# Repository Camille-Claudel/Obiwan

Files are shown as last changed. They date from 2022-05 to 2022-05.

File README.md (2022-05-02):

# Introduction
Obiwan est un pointeur laser capable de s’orienter dans n’importe quelle direction.  

https://user-images.githubusercontent.com/80780126/166306557-4985dba1-e16e-4158-aaa8-b6b7efb4e9a4.mp4

## Contexte
Nous sommes le club d'informatique du lycée Camille Claudel avec environ 8 membres actifs. Étant un club très jeune et géré exclusivement par des élèves, nous sommes fiers de vous présenter ce projet, fait en quelques semaines avec un budget très réduit. Nous espérons que vous apprécierez lire cette présentation autant que nous avons apprécié réaliser ce projet !

## Objectifs
L’objectif principal est de pouvoir orienter le laser dans une direction arbitraire.  
Nous espérons ensuite pouvoir utiliser le dispositif pour dessiner un motif et le capturer à l’aide d’une photo à pose longue, à la manière du [light painting](https://fr.wikipedia.org/wiki/Light_painting).  
Enfin, si tous les objectifs précédents sont remplis, nous essayerons d’automatiser le contrôle du laser pour dessiner un motif à partir d’une image vectorielle.

# Principe de fonctionnement
Pour diriger le laser, nous utiliserons deux moteurs: l’un qui contrôle le mouvement gauche-droite, appelé azimut, et l’autre qui contrôle l'axe haut-bas, appelé altitude. Ce vocabulaire est emprunté au système de coordonnées céleste appelé “[système de coordonnées horizontales](https://fr.wikipedia.org/wiki/Syst%C3%A8me_de_coordonn%C3%A9es_horizontales)”, utilisé en astronomie:  
  
Pour photographier les motifs créés, nous utiliserons la technique du light painting. Elle consiste à prendre une photo avec un temps de pose (la durée pendant laquelle l’appareil photo capte de la lumière) relativement long, pour faire apparaître sur l’image la trajectoire du point lumineux.

# Problèmes rencontrés et solutions apportées

## Choix de fabrication/architecture
Le mouvement est contrôlé par des servomoteurs et une carte Arduino. Le moteur azimut entraîne une roue d’engrenage sur laquelle est positionné le moteur altitude. Le laser est scotché sur le moteur altitude. La structure est imprimée en 3D en PLA.  

  
Le moteur altitude est positionné au centre le son engrenage, ce qui fait que le laser a une excentricité par rapport à l’axe azimutal. La droite du rayon du laser n’est donc pas sécante avec l’axe de rotation azimutal.

## Excentricité
Cette excentricité conduit les dessins à être déformés. Pour y remédier, le programme prend en entrée les coordonnées du point visé, et calcule l’angle à donner aux moteurs pour le pointer malgré l’excentricité.  



## Précision
Au départ, nous dessinions sur un mur à environ 1.5m du laser. Le tracé manquait cependant de précision, car nos moteurs ont une précision de seulement environ 1 degré. Nous avons donc d’abord réduit la taille de l’engrenage de l’axe azimutal pour avoir une réduction 1:2, et ainsi avoir une précision de 0.5 degré. Cela a eu pour effet secondaire de rendre le dispositif plus compact.  

  
Cela n’a pas suffi à régler le problème, car la précision de l’axe altitude est restée la même, et même ces 0.5 degrés de précisions n’étaient pas suffisants. Nous avons alors réalisé que simplement rapprocher le dispositif de la surface de dessin augmentait grandement la précision, car les dessins faisaient alors plus de degrés de large.

## Rectilinéarité

Avec notre dispositif, nous pouvions pointer une position donnée, mais lors du déplacement d’une position à une autre le tracé n’était pas droit, car la vitesse des moteurs n’est pas constante. Pour tracer des segments, on pointe donc vers des positions intermédiaires.

En ajoutant plus de points intermédiaires, les traits sont plus rectilignes et plus uniformes.


# Résultat final


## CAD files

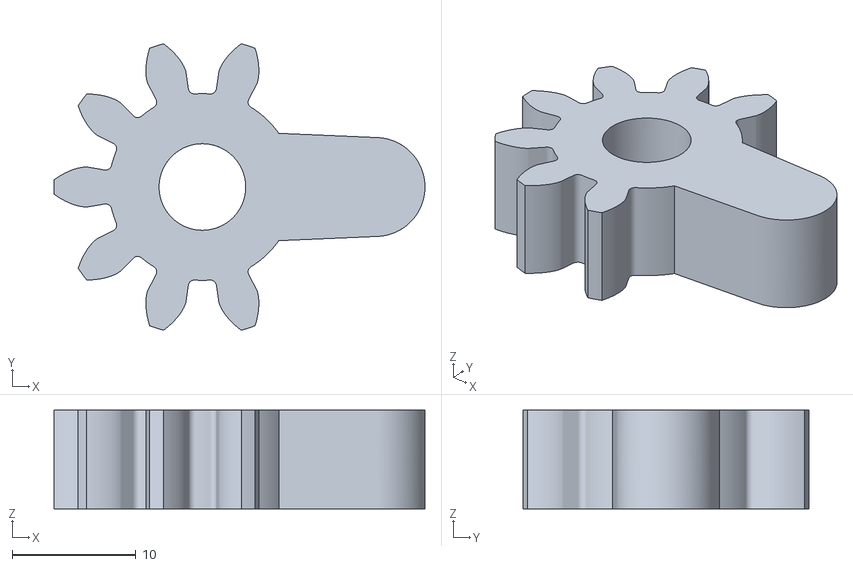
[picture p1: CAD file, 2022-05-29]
main wheel.stl
30.0 x 23.2 x 8.00

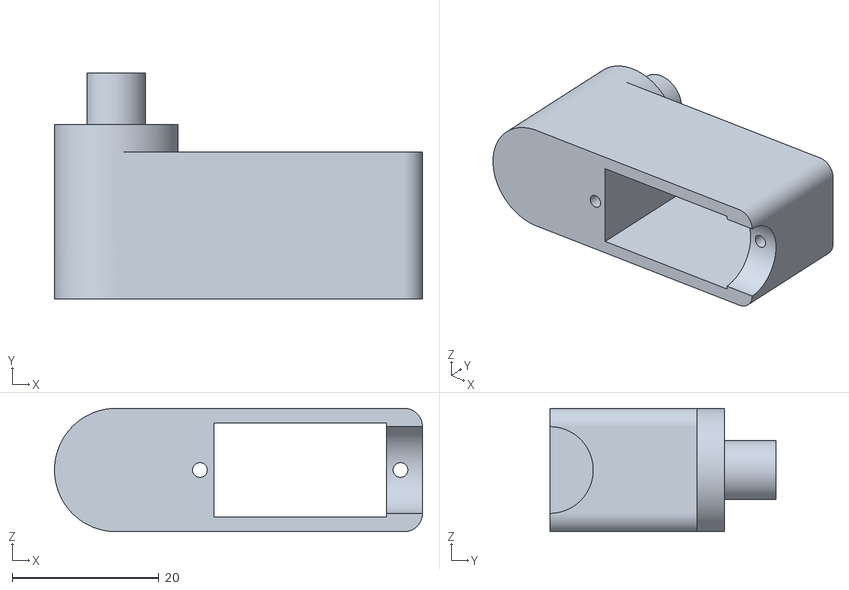
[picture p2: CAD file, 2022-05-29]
base.stl
50.1 x 30.8 x 16.8

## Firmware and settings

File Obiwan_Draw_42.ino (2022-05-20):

#include <Servo.h>

Servo sx;
Servo sy;
double d = 9;
double e = 2;
double cx=0;//current x
double cy=0;//curent y

void setxy(double x, double y)
{
  cx=x;
  cy=y;
  sx.write(90 + 2*degrees(atan2(x, d)+asin(e/sqrt(sq(d)+sq(x)))));
  sy.write(95 - degrees(atan2(y, sqrt(sq(d) + sq(x) - sq(e)))));
}

void getcircular(double r, double angle, double &x, double &y) {
  x = cos(radians(angle)) * r;
  y = sin(radians(angle)) * r;
}

void drawline(double x,double y, int stops){
  double x0=cx;
  double y0=cy;
  for (int i=1; i<=stops; i++){
    double xd= (i*x+(stops-i)*x0)/stops;
    double yd= (i*y+(stops-i)*y0)/stops;
    setxy(xd,yd);
    delay(30);
  }
}

void drawpentagram(double r,double x0, double y0){
  double x = 0;
  double y = 0;
  for (int i = 144; i <= 720; i += 144){
    getcircular(r,i,x,y);
    drawline(x+x0,y+y0,20);
    //Serial.println("hey j'ai fait une ligne");
  }
}
void drawcircle(double r,double x0, double y0){
  double x = 0;
  double y = 0;
  for (int i = 0; i < 360; i += 1){
    getcircular(r,i,x,y);
    setxy(x,y);
    delay(10);
    Serial.println("hey j'ai fait un degré");
  }
}

int kEnDePos[] = {
0, 0,
34, 2,
0, 1,
34, 18,
20, 18,
20, 24,
34, 69,
41, 68,
41, 24,
50, 24,
50, 18,
41, 18,
41, 2,
0, 0,
34, 24,
0, 1,
11, 24,
34, 56,
34, 24,
0, 0,
59, 2,
0, 1,
59, 14,
68, 25,
78, 33,
89, 45,
89, 56,
84, 62,
71, 62,
60, 54,
60, 63,
70, 69,
85, 69,
93, 65,
97, 56,
97, 44,
86, 30,
75, 22,
68, 15,
67, 9,
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
};

//           pos x       , pos y        , size 
void kEnDe(double setupX, double setupY, double setupS) {
  
  for (int i = 0; i<88; i += 2){
    //Serial.println(i .. " [" .. kEnDePos[i] .. "," .. kEnDePos[i + 1] .. "]" );
    if (kEnDePos[i] == 0) {
      if (kEnDePos[i+1] == 0) {
        digitalWrite(4,HIGH);
        delay(300);
      }
      else {
        digitalWrite(4,LOW);
        delay(300);
      }
    }
    else{
      /*Serial.print("\n Info ");
      Serial.print(i);
      Serial.print(" : ");
      Serial.print(kEnDePos[i]);
      Serial.print(" , ");
      Serial.print(kEnDePos[i + 1]);*/
      setxy((setupX + kEnDePos[i]) * setupS , (setupY + kEnDePos[i + 1])* setupS ); 
    }
  }
}


void setup() {
  sx.attach(2);
  sy.attach(3);
  pinMode(4,OUTPUT);
  setxy(0,0);
  //delay(5000);
  //Serial.begin(9600);
}

void loop() {
  kEnDe(-40,-40,0.1);
  delay(100);
  //drawpentagram(4, 0, .5);
  //drawcircle(4, 0, .5);
  
  //Serial.println("hey j'ai fait un pentagram");
  

}
